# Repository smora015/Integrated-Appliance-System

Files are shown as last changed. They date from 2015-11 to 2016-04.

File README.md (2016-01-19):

# Integrated-Appliance-System
##### Controllers for an Energy Efficient, Sustainable Appliance System.

The Integrated Appliance System is a Senior Design, or capstone project for the Department of Chemical & Environmental Engineering for UC Riverside, under the advisory of Dr. Kawai Tam. We aim to draft, design, and potentially market an energy combination of appliances that cut your electricity bill substantially. It's common knowledge that appliances such as washers and dryers in typical residential homes are among the highest in terms of energy consumption. We're an interdisciplinary team that consists of Chemical, Environmental, Mechanical, and Computer Engineering majors. In a nut shell, the design utilizes solar thermal energy to heat up clothes, and taking the surplus energy to be routed into a water heater or into a home as warm air for heating, thus replacing a clothes dryer, water heater, and space heater. Being pretty savvy in embedded systems, I was reached out to implement a control system for the appliances. 

### Subsystems

##### IAS-PCB
Collection of Eagle PCB CAD files that contain prototype/production-ready schematic and board layouts for the IAS.

##### Integrated Appliance System
Contains the Atmel Project source for the ATmega1284-PU work.

##### Raspberry-Pi-Logger
Contains logic for a temporary method of controlling the IAS, utilizing startup scripts to log temperature and humidity data.

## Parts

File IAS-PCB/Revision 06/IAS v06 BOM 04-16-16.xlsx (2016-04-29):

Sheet: PCB BOM
Index | Store | Store Part # | Manufacturer Part # | Description | Device Packaging | Qty | Unit Price | Price | Comments
1 | Digikey | ATMEGA1284-PU-ND | ATMEGA1284-PU | Atmega1284 Microcontroller | Through-hole | 2 | $7.60 | $15.20 | Main Controllers
2 | Digikey | 296-1600-5-ND | 296-1600-5-ND | 8-bit Shift Register | Through-hole | 1 | $0.58 | $0.58 | Used to reduce amount of pins needed
3 | Digikey | 311-10KERCT-ND | RC1206JR-0710KL | 10K Ohm Resistor | 1206 | 2 | $0.10 | $0.20 | Pull-up resistors for Sensors
4 | Digikey | 311-1.00KFRCT-ND | RC1206FR-071KL | 1K Ohm Resistor | 1206 | 2 | $0.03 | $0.06 | Used for Bluetooth RX pin as voltage divider | `
5 | Digikey | 311-2.0KERCT-ND | RC1206JR-072KL | 2K Ohm Resistor | 1206 | 1 | $0.02 | $0.02 | Used for Bluetooth RX pin as voltage divider
6 | Digikey | 311-1356-1-ND | CC1206KKX7R8BB105 | 1 uF 25V Capacitor | 1206 | 2 | $0.12 | $0.24 | Stabilizes input voltage/current
7 | Digikey | 587-1353-1-ND | TMK316F106ZL-T | 10uF 25V Capacitor | 1206 | 2 | $0.26 | $0.51 | Stabilizes regulated voltage/current
8 | Digikey | 296-9213-5-ND | CD74HC4050E | 5V to 3.3V Level Shifter | 16DIP | 1 | $0.48 | $0.48 | Converts power to 3.3V for Nokia LCD
9 | Digikey | S7006-ND | PPTC081LFBN-RC | 8-pin header | Through-hole .1" | 7 | $0.66 | $4.65 | Header pins for component connections
10 | Digikey | S7004-ND | PPTC061LFBN-RC | 6-pin header | Through-hole .1" | 2 | $0.68 | $1.36 | Header pins for component connections
11 | Digikey | S7038-ND | PPPC051LFBN-RC | 5-pin header | Through-hole .1" | 2 | $0.65 | $1.30 | Header pins for component connections
12 | Digikey | S7002-ND | PPTC041LFBN-RC | 4-pin header | Through-hole .1" | 4 | $0.46 | $1.85 | Header pins for component connections
14 | Digikey | AZ1117EH-5.0TRG1DICT-ND | AZ1117EH-5.0TRG1 | 5V Fixed Voltage Regulator (16V Max Input @ 1A) | SOT-223 | 1 | $0.43 | $0.43 | Input regulator (5V)
15 | Digikey | CP-102A-ND | PJ-102B | 2.0mm DC barrel-power jack | Through-hole | 1 | $1.00 | $1.00 | Connector jack for power
16 | Digikey | 754-1724-ND | WP710A10SGD5V | Power Status LED | Through-hole | 1 | $0.44 | $0.44 | LED indicator for power on
17 | Digikey | AE9992-ND | A16-LC-TT | 16-DIP Socket | Through-hole | 2 | $0.25 | $0.50 | Allows non-solder connections for chips
18 | Digikey | 609-4716-ND | DILB40P-223TLF | 40-DIP Socket | Through-hole | 2 | $0.58 | $1.16 | Allows non-solder connections for chips
19 | OSH Park | N/A | OSHPark.com | PCB Board Manufacturing (3.54x2.30 inches) | 2-layer PCB | 1 | $40.65 | $40.65 | 3 Boards Included
 |  |  |  | Total |  |  |  | $70.63

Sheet: System BOM
Index | Store | Store Part # | Manufacturer Part # | Description | Device Packaging | Qty | Unit Price | Price | Comments | Remark
A | Amazon | Here (http://www.amazon.com/Nokia-5110-LCD-Screen/dp/B0068EUIXG) | 5110 | Nokia 5110 LCD | N/A | 1 | $6.60 | $6.60 | 5V IAS Controls Display | -
B | Amazon | Here (http://www.amazon.com/uxcell-Standard-Character-Backlight-Display/dp/B00EDMMTGY) | uxcell | 16x2 Backlit LCD | N/A | 1 | $7.69 | $7.69 | 5V IAS Status Display | -
C | Amazon | Here (http://www.amazon.com/gp/product/B00R4KGG6Q?psc=1&redirect=true&ref_=oh_aui_detailpage_o05_s00) | HT21 AM2301 | Temperature & Humidity Sensor | N/A | 3 | $8.60 | $25.80 | 5V Sensor with -40 - 80 deg C Range | Alternative - DHT 22
D | Amazon | Here (http://www.amazon.com/RioRand-Waterproof-Digital-Temperature-DS18b20/dp/B00KUNKR3M) | DS18B20 | Temperature Probe | N/A | 2 | $5.00 | $10.00 | 5V Sensor with -55 - 125 deg C Range | Optional
E | Amazon | Here (http://www.amazon.com/2013newestseller-HC-SR501-Pyroelectric-Infrared-Detector/dp/B00FDPO9B8) | PIR | Motion Sensor | N/A | 4 | $2.00 | $8.00 | 5V Sensor | -
F | Parallax | Here (https://www.parallax.com/product/27115) | SRD-05VDC | Relay Switch | N/A | 4 | $10.00 | $40.00 | Switch to power on fans | Find better price!
G | Amazon | Here (http://www.amazon.com/uxcell-Matrix-Keyboard-Keypad-Stamp/dp/B00HGAK2FK) | uxcell | Keypad | N/A | 1 | $4.00 | $4.00 | Keypad to control | -
H | Amazon | Here (http://www.amazon.com/JY-MCU-Arduino-Bluetooth-Wireless-Serial/dp/B009DZQ4MG) | JY-MCU | Bluetooth Wireless module | N/A | 1 | $6.50 | $6.50 | Allows for wireless control of IAS | -
 |  |  |  |  |  |  |  | $0.00
 |  |  |  |  |  |  |  | $0.00
 |  |  |  |  |  |  |  | $0.00
 |  |  |  |  |  |  |  | $0.00
 |  |  |  |  |  |  |  | $0.00
 |  |  |  |  |  |  |  | $0.00
 |  |  |  |  |  |  |  | $0.00
 |  |  |  |  |  |  |  | $0.00
 |  |  |  |  |  |  |  | $0.00
 |  |  |  |  |  |  |  | $0.00
 |  |  |  |  |  |  |  | $0.00
 |  |  |  |  |  |  |  | $0.00
 |  |  |  |  |  |  |  | $0.00
 |  |  |  |  |  |  |  | $0.00
 |  |  |  |  |  |  |  | $0.00
 |  |  |  |  |  |  |  | $0.00
 |  |  |  |  |  |  |  | $0.00
 |  |  |  |  |  |  |  | $0.00
 |  |  |  |  |  |  |  | $0.00
 |  |  |  |  |  |  |  | $0.00

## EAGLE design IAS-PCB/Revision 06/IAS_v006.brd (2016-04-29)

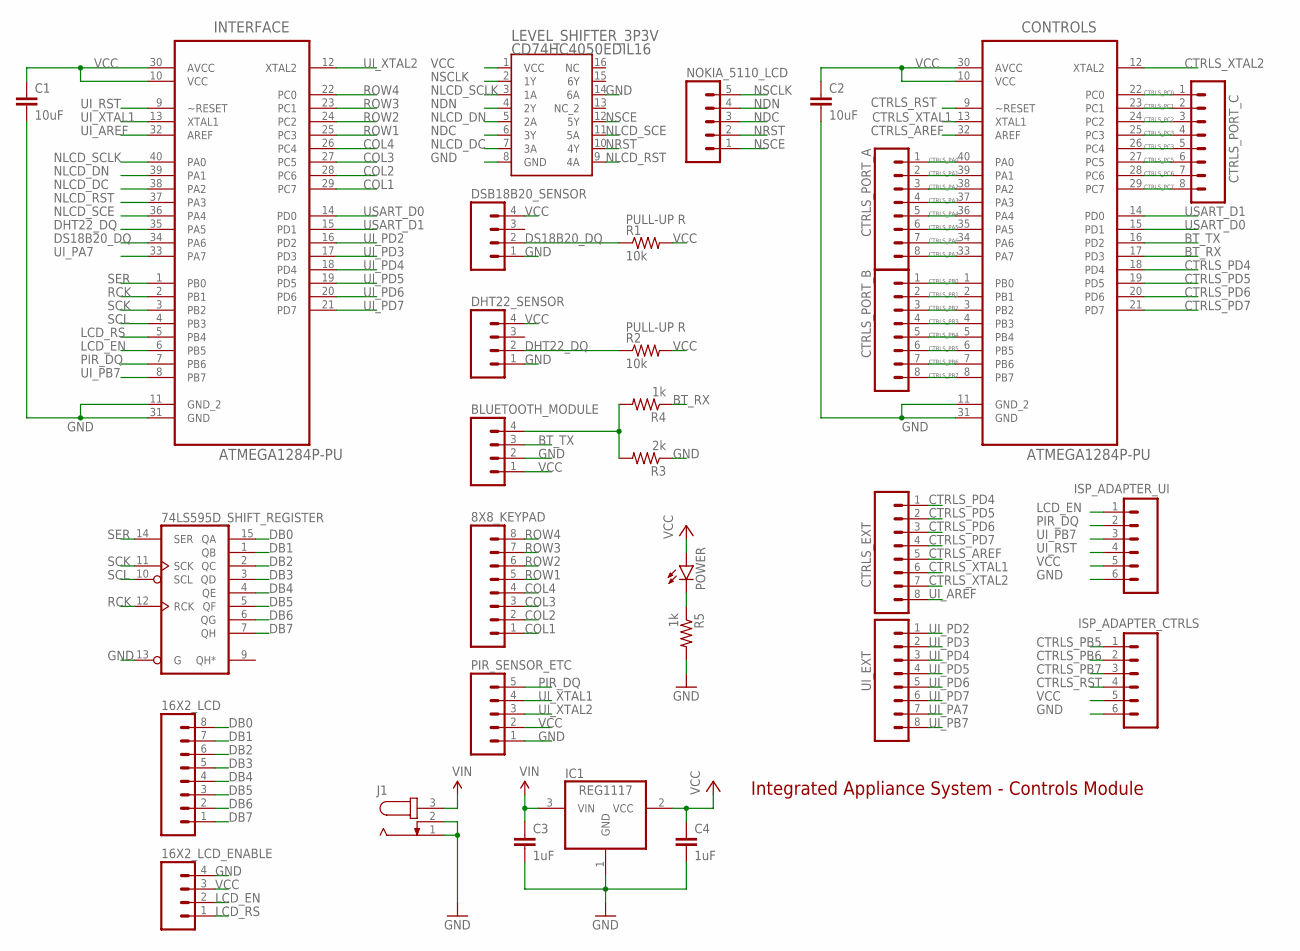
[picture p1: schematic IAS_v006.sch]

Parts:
8X8_KEYPAD, 16X2_LCD: M08; 1X08_ROUND
16X2_LCD_ENABLE: M04NO_SILK_ALL_ROUND; 1X04_NO_SILK_ALL_ROUND
74LS595D_SHIFT_REGISTER: 74LS595N; DIL16; MPN SN74LS595D
BLUETOOTH_MODULE: M04NO_SILK_ALL_ROUND; 1X04_NO_SILK_ALL_ROUND
C1, C2: 10uF; 1206
C3, C4: 1uF; 1206
CONTROLS: ATMEGA1284P-PU; DIP254P1524X483-40
CTRLS_EXT: M08; 1X08_ROUND
CTRLS_PORT_A: M08; 1X08_ROUND
CTRLS_PORT_B: M08; 1X08_ROUND
CTRLS_PORT_C: M08; 1X08_ROUND
DHT22_SENSOR: M04NO_SILK_ALL_ROUND; 1X04_NO_SILK_ALL_ROUND
DSB18B20_SENSOR: M04NO_SILK_ALL_ROUND; 1X04_NO_SILK_ALL_ROUND
IC1: REG1117; SOT223
INTERFACE: ATMEGA1284P-PU; DIP254P1524X483-40
ISP_ADAPTER_CTRLS: M06SILK_FEMALE_PTH; 1X06
ISP_ADAPTER_UI: M06SILK_FEMALE_PTH; 1X06
J1: JACK-PLUG0; SPC4077
LEVEL_SHIFTER_3P3V: CD74HC4050EDIL16; DIL16
NOKIA_5110_LCD: M05PTH; 1X05
PIR_SENSOR_ETC: M05PTH; 1X05
POWER: LED3MM
R1, R2: 10k; 1206
R3: 2k; 1206
R4, R5: 1k; 1206
UI_EXT: M08; 1X08_ROUND

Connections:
BT_RX: CONTROLS.17 (PD3), R4.1
BT_TX: BLUETOOTH_MODULE.3, CONTROLS.16 (PD2)
COL1: 8X8_KEYPAD.1, INTERFACE.29 (PC7)
COL2: 8X8_KEYPAD.2, INTERFACE.28 (PC6)
COL3: 8X8_KEYPAD.3, INTERFACE.27 (PC5)
COL4: 8X8_KEYPAD.4, INTERFACE.26 (PC4)
CTRLS_AREF: CONTROLS.32 (AREF), CTRLS_EXT.5
CTRLS_PA0: CONTROLS.40 (PA0), CTRLS_PORT_A.1
CTRLS_PA1: CONTROLS.39 (PA1), CTRLS_PORT_A.2
CTRLS_PA2: CONTROLS.38 (PA2), CTRLS_PORT_A.3
CTRLS_PA3: CONTROLS.37 (PA3), CTRLS_PORT_A.4
CTRLS_PA4: CONTROLS.36 (PA4), CTRLS_PORT_A.5
CTRLS_PA5: CONTROLS.35 (PA5), CTRLS_PORT_A.6
CTRLS_PA6: CONTROLS.34 (PA6), CTRLS_PORT_A.7
CTRLS_PA7: CONTROLS.33 (PA7), CTRLS_PORT_A.8
CTRLS_PB0: CONTROLS.1 (PB0), CTRLS_PORT_B.1
CTRLS_PB1: CONTROLS.2 (PB1), CTRLS_PORT_B.2
CTRLS_PB2: CONTROLS.3 (PB2), CTRLS_PORT_B.3
CTRLS_PB3: CONTROLS.4 (PB3), CTRLS_PORT_B.4
CTRLS_PB4: CONTROLS.5 (PB4), CTRLS_PORT_B.5
CTRLS_PB5: CONTROLS.6 (PB5), CTRLS_PORT_B.6, ISP_ADAPTER_CTRLS.1
CTRLS_PB6: CONTROLS.7 (PB6), CTRLS_PORT_B.7, ISP_ADAPTER_CTRLS.2
CTRLS_PB7: CONTROLS.8 (PB7), CTRLS_PORT_B.8, ISP_ADAPTER_CTRLS.3
CTRLS_PC0: CONTROLS.22 (PC0), CTRLS_PORT_C.1
CTRLS_PC1: CONTROLS.23 (PC1), CTRLS_PORT_C.2
CTRLS_PC2: CONTROLS.24 (PC2), CTRLS_PORT_C.3
CTRLS_PC3: CONTROLS.25 (PC3), CTRLS_PORT_C.4
CTRLS_PC4: CONTROLS.26 (PC4), CTRLS_PORT_C.5
CTRLS_PC5: CONTROLS.27 (PC5), CTRLS_PORT_C.6
CTRLS_PC6: CONTROLS.28 (PC6), CTRLS_PORT_C.7
CTRLS_PC7: CONTROLS.29 (PC7), CTRLS_PORT_C.8
CTRLS_PD4: CONTROLS.18 (PD4), CTRLS_EXT.1
CTRLS_PD5: CONTROLS.19 (PD5), CTRLS_EXT.2
CTRLS_PD6: CONTROLS.20 (PD6), CTRLS_EXT.3
CTRLS_PD7: CONTROLS.21 (PD7), CTRLS_EXT.4
CTRLS_RST: CONTROLS.9 (~RESET), ISP_ADAPTER_CTRLS.4
CTRLS_XTAL1: CONTROLS.13 (XTAL1), CTRLS_EXT.6
CTRLS_XTAL2: CONTROLS.12 (XTAL2), CTRLS_EXT.7
DB0: 16X2_LCD.8, 74LS595D_SHIFT_REGISTER.15 (QA)
DB1: 16X2_LCD.7, 74LS595D_SHIFT_REGISTER.1 (QB)
DB2: 16X2_LCD.6, 74LS595D_SHIFT_REGISTER.2 (QC)
DB3: 16X2_LCD.5, 74LS595D_SHIFT_REGISTER.3 (QD)
DB4: 16X2_LCD.4, 74LS595D_SHIFT_REGISTER.4 (QE)
DB5: 16X2_LCD.3, 74LS595D_SHIFT_REGISTER.5 (QF)
DB6: 16X2_LCD.2, 74LS595D_SHIFT_REGISTER.6 (QG)
DB7: 16X2_LCD.1, 74LS595D_SHIFT_REGISTER.7 (QH)
DHT22_DQ: DHT22_SENSOR.2, INTERFACE.35 (PA5), R2.1
DS18B20_DQ: DSB18B20_SENSOR.2, INTERFACE.34 (PA6), R1.1
GND: 16X2_LCD_ENABLE.4, 74LS595D_SHIFT_REGISTER.8 (GND), 74LS595D_SHIFT_REGISTER.13 (G), BLUETOOTH_MODULE.2, C1.2, C2.2, C3.2, C4.2, CONTROLS.11 (GND_2), CONTROLS.31 (GND), DHT22_SENSOR.1, DSB18B20_SENSOR.1, IC1.1 (GND), INTERFACE.11 (GND_2), INTERFACE.31 (GND), ISP_ADAPTER_CTRLS.6, ISP_ADAPTER_UI.6, J1.1, J1.2, LEVEL_SHIFTER_3P3V.8 (GND), LEVEL_SHIFTER_3P3V.14 (6A), PIR_SENSOR_ETC.1, R3.1, R5.2
LCD_EN: 16X2_LCD_ENABLE.2, INTERFACE.6 (PB5), ISP_ADAPTER_UI.1
LCD_RS: 16X2_LCD_ENABLE.1, INTERFACE.5 (PB4)
unnamed: POWER.K (C), R5.1
unnamed: BLUETOOTH_MODULE.4, R3.2, R4.2
NDC: LEVEL_SHIFTER_3P3V.6 (3Y), NOKIA_5110_LCD.3
NDN: LEVEL_SHIFTER_3P3V.4 (2Y), NOKIA_5110_LCD.4
NLCD_DC: INTERFACE.38 (PA2), LEVEL_SHIFTER_3P3V.7 (3A)
NLCD_DN: INTERFACE.39 (PA1), LEVEL_SHIFTER_3P3V.5 (2A)
NLCD_RST: INTERFACE.37 (PA3), LEVEL_SHIFTER_3P3V.9 (4A)
NLCD_SCE: INTERFACE.36 (PA4), LEVEL_SHIFTER_3P3V.11 (5A)
NLCD_SCLK: INTERFACE.40 (PA0), LEVEL_SHIFTER_3P3V.3 (1A)
NRST: LEVEL_SHIFTER_3P3V.10 (4Y), NOKIA_5110_LCD.2
NSCE: LEVEL_SHIFTER_3P3V.12 (5Y), NOKIA_5110_LCD.1
NSCLK: LEVEL_SHIFTER_3P3V.2 (1Y), NOKIA_5110_LCD.5
PIR_DQ: INTERFACE.7 (PB6), ISP_ADAPTER_UI.2, PIR_SENSOR_ETC.5
RCK: 74LS595D_SHIFT_REGISTER.12 (RCK), INTERFACE.2 (PB1)
ROW1: 8X8_KEYPAD.5, INTERFACE.25 (PC3)
ROW2: 8X8_KEYPAD.6, INTERFACE.24 (PC2)
ROW3: 8X8_KEYPAD.7, INTERFACE.23 (PC1)
ROW4: 8X8_KEYPAD.8, INTERFACE.22 (PC0)
SCK: 74LS595D_SHIFT_REGISTER.11 (SCK), INTERFACE.3 (PB2)
SCL: 74LS595D_SHIFT_REGISTER.10 (SCL), INTERFACE.4 (PB3)
SER: 74LS595D_SHIFT_REGISTER.14 (SER), INTERFACE.1 (PB0)
UI_AREF: CTRLS_EXT.8, INTERFACE.32 (AREF)
UI_PA7: INTERFACE.33 (PA7), UI_EXT.7
UI_PB7: INTERFACE.8 (PB7), ISP_ADAPTER_UI.3, UI_EXT.8
UI_PD2: INTERFACE.16 (PD2), UI_EXT.1
UI_PD3: INTERFACE.17 (PD3), UI_EXT.2
UI_PD4: INTERFACE.18 (PD4), UI_EXT.3
UI_PD5: INTERFACE.19 (PD5), UI_EXT.4
UI_PD6: INTERFACE.20 (PD6), UI_EXT.5
UI_PD7: INTERFACE.21 (PD7), UI_EXT.6
UI_RST: INTERFACE.9 (~RESET), ISP_ADAPTER_UI.4
UI_XTAL1: INTERFACE.13 (XTAL1), PIR_SENSOR_ETC.4
UI_XTAL2: INTERFACE.12 (XTAL2), PIR_SENSOR_ETC.3
USART_D0: CONTROLS.15 (PD1), INTERFACE.14 (PD0)
USART_D1: CONTROLS.14 (PD0), INTERFACE.15 (PD1)
VCC: 16X2_LCD_ENABLE.3, 74LS595D_SHIFT_REGISTER.16 (VCC), BLUETOOTH_MODULE.1, C1.1, C2.1, C4.1, CONTROLS.10 (VCC), CONTROLS.30 (AVCC), DHT22_SENSOR.4, DSB18B20_SENSOR.4, IC1.2 (VCC), INTERFACE.10 (VCC), INTERFACE.30 (AVCC), ISP_ADAPTER_CTRLS.5, ISP_ADAPTER_UI.5, LEVEL_SHIFTER_3P3V.1 (VCC), PIR_SENSOR_ETC.2, POWER.A, R1.2, R2.2
VIN: C3.1, IC1.3 (VIN), J1.3

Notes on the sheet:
PULL-UP R
Integrated Appliance System - Controls Module

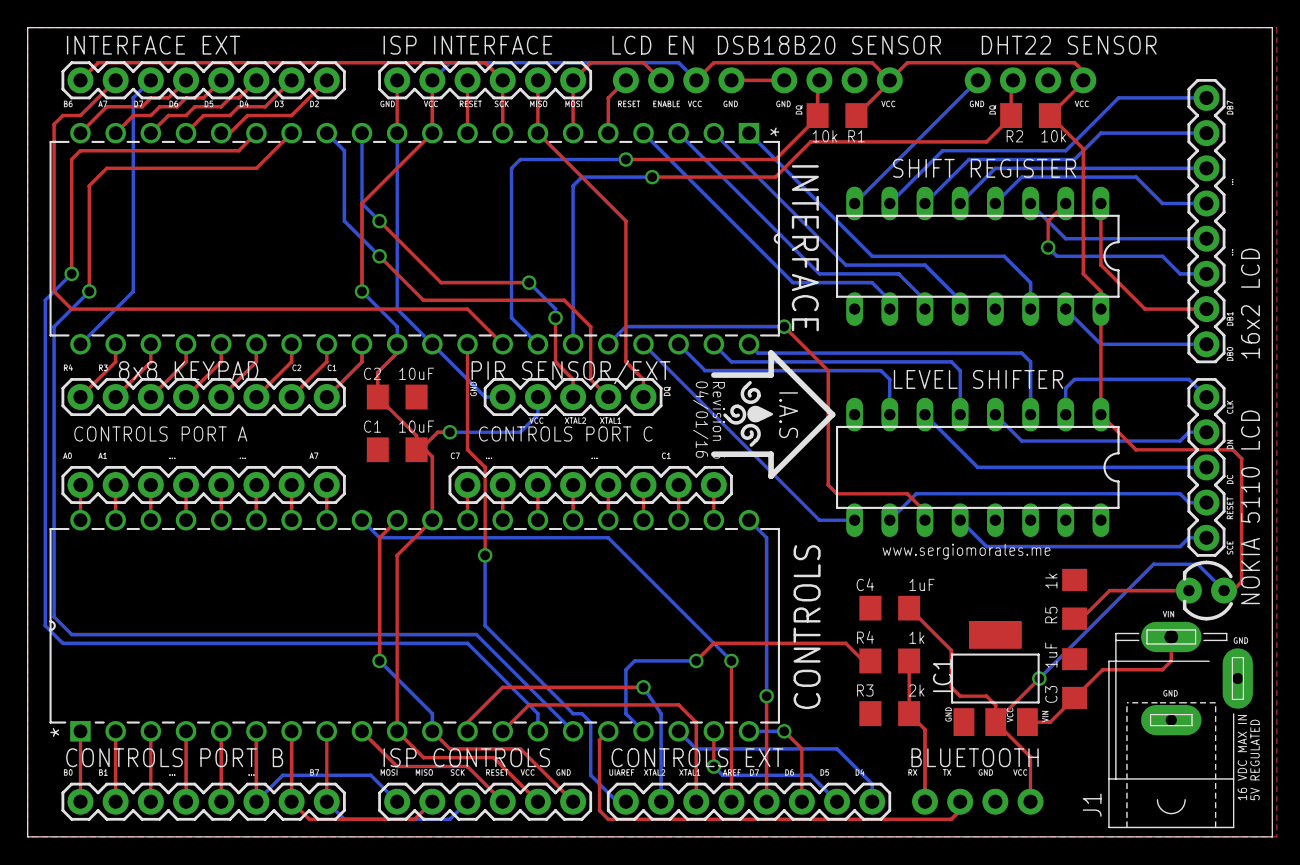
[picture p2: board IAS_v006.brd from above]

Board: 2 copper layers, 89.8 x 58.4 mm, 31 parts (0 on the bottom side), 88 nets.

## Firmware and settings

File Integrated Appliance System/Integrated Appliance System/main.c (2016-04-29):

#include <stdint.h> 
#include <stdlib.h> 
#include <stdio.h> 
#include <stdbool.h> 
#include <string.h> 
#include <math.h> 

// AVR Include Files
#define F_CPU 8000000UL     // 8Mhz Clock
#include <util/delay.h>
#include <avr/io.h>         
#include <avr/interrupt.h> 
#include <avr/eeprom.h> 
#include <avr/portpins.h> 
#include <avr/pgmspace.h> 

// IAS macro and pinout definitions
#include "ias_pinout.h"
#include "display/lumex_lcd.h"
#include "com/shift_reg.h"

int main(void) 
{
	DDRA = 0xFF; PORTA = 0x00; // Nokia LCD: 0-4. DHT22: 5. DS18B20: 6.
	DDRB = 0xFF; PORTB = 0x00; // 16x2 LCD on Shift Registers
	DDRC = 0xF0; PORTC = 0x0F; // Keypad
	DDRD = 0xFF; PORTD = 0x00; // USART interface
	
    LCD_init();

	for(;;)
	{
		LCD_DisplayString(3, (const unsigned char*) "Hello World!", 0);
        
        //_delay_ms(1000);       // Delay logic for 100 ms
		
		//PORTD ^= 0xFF; // UI PORTD bits
			
	}
		
	return 0; 
}


//// FreeRTOS Include Files
//#include "FreeRTOS.h"
//#include "task.h"
//#include "croutine.h"
//#include "usart_ATmega1284.h"

//void ControlTask()
//{
//for( ;; )
//{
//Control_Tick();
//vTaskDelay(1);
//}
//}
//
//void StartSecPulse(unsigned portBASE_TYPE Priority)
//{
//xTaskCreate(ControlTask, (signed portCHAR *)"ControlTask", configMINIMAL_STACK_SIZE, NULL, Priority, NULL );
//}

	//#ifdef main2
	//DDRB = 0xFF; PORTB = 0x00; // Fans (0)
	//DDRC = 0xFF; PORTC = 0x00; // LEDS
	//DDRA = 0xFF; PORTA = 0x00; // Motor
	//initUSART(1);			   // Bluetooth
	//initUSART(0);			   // IAS
	//USART_Flush(0);
	//USART_Flush(1);
	//
	//// Start Tasks
	//StartSecPulse(1);
	//
	//// Run Scheduler
	//vTaskStartScheduler();
	//#else
	//DDRA = 0xFF; PORTA = 0x00; // Nokia LCD: 0-4. DHT22: 5. DS18B20: 6.
	//DDRB = 0xFF; PORTB = 0x00; // 16x2 LCD on Shift Registers
	//DDRC = 0xF0; PORTC = 0x0F; // Keypad
	//DDRD = 0xFF; PORTD = 0x00; // USART interface
	//
	//while(1)
	//{
	//
	//IAS_MenuTick();
	//_delay_ms(1);
	//}
	//#endif

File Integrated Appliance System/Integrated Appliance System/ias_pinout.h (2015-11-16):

/*
 * ias_pinout.h
 *
 * Created: 10/12/2015 9:33:00 PM
 *  Author: Sergio
 *
 *  Description: Defines the pinout for all ports 
 */ 



#ifndef IAS_PINOUT_H_
#define IAS_PINOUT_H_
    
    #include <avr/io.h>
    
    /* ============== Communication ============== */

    // 4x4 Keypad { keypad.h }
    #define KEYPADPORT PORTC
    #define KEYPADPIN  PINC
    #define ROW1 3
    #define ROW2 2
    #define ROW3 1
    #define ROW4 0
    #define COL1 7
    #define COL2 6
    #define COL3 5
    #define COL4 4

    // Shift Register { shift_reg.h }
    #define SHIFT_PORT PORTB
    #define SER_PIN   0
    #define RCLK_PIN  1
    #define SRCLK_PIN 2
    #define SRCLR_PIN 3

    /* ============== Sensors ============== */

    // DHT22 Temp/Humidity Sensor { dht22.h }
    #define DHT_DDR DDRA
    #define DHT_PORT PORTA
    #define DHT_PIN PINA
    #define DHT_INPUTPIN 5

    // DS18B20 Temperature Probe { ds18b20.h }
    #define DS18B20_PORT PORTA
    #define DS18B20_DDR  DDRA
    #define DS18B20_PIN  PINA
    #define DS18B20_DQ   6
    
    // PIR Motion Sensor { pir.h }
    #define PIR_DDR  DDRB
    #define PIR_READ PINB
    #define PIR_PIN  6

    /* ============== Display ============== */

    // 16x2 LUMEX LCD { lumex_lcd.h }
    //#define DATA_BUS PORTB          // port connected to pins 7-14 of LCD display | WE NOW USE SHIFT REGISTERS ON DEFINED PINS
    #define CONTROL_BUS PORTB	      // port connected to pins 4 and 6 of LCD disp.
    #define RS 4			          // pin number of uC connected to pin 4 of LCD disp.
    #define E 5			              // pin number of uC connected to pin 6 of LCD disp.

    // NOKIA 84x48 PCD8544 LCD { pcd8544.h }
    #define LCD_PORT            PORTA
    #define LCD_SCE_HI			LCD_PORT |= (1<<4)
    #define LCD_SCE_LO			LCD_PORT &= ~(1<<4)
    #define LCD_RST_HI			LCD_PORT |= (1<<3)
    #define LCD_RST_LO			LCD_PORT &= ~(1<<3)
    #define LCD_DC_HI			LCD_PORT |= (1<<2)
    #define LCD_DC_LO			LCD_PORT &= ~(1<<2)
    #define LCD_DN_HI			LCD_PORT |= (1<<1)
    #define LCD_DN_LO			LCD_PORT &= ~(1<<1)
    #define LCD_SCLK_HI			LCD_PORT |= (1<<0)
    #define LCD_SCLK_LO			LCD_PORT &= ~(1<<0)
    //#define LCD_BACKLIGHT_HI	LCD_PORT |= (1<<5)   // Optional
    //#define LCD_BACKLIGHT_LO	LCD_PORT &= ~(1<<5)  // Optional
    
    #define LCD_C 0 // Command
    #define LCD_D 1 // Data

    #define LCD_WIDTH	84
    #define LCD_HEIGHT	48

#endif /* IAS_PINOUT_H_ */

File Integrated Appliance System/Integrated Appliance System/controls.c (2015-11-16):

/*
 * controls.c
 *
 * Created: 12/15/2014 7:00:38 PM
 *  Author: Sergio
 */ 
#include "controls.h"
#include "com/usart_ATmega1284.h"
#include <avr/io.h>
#include <stdlib.h>

unsigned char step_count = 0x00;
unsigned char  steps[8] = { 0x01, 0x03, 0x02, 0x06, 0x04, 0x0C, 0x08, 0x09 };	// Clockwise phases
unsigned char bsteps[8] = { 0x09, 0x08, 0x0C, 0x04, 0x06, 0x02, 0x03, 0x01  };  // Counter-Clockwise phases
int count = 0;																	// Counter for number of phases

char temp;
char message[100];

void USART_send_string( const char* string )
{
	USART_Flush(1);
	USART_Flush(0);
	int index = 0;
	while( string[index] )
	{
		USART_Send(string[index], 1);
		++index;
	}
}

enum control_states { init, receive, actuate_gears, disable_gears, actuate_fans, disable_fans, send_report } control_state;
void Control_Tick()
{
	// Mealy FSM (actions and transitions)
	switch( control_state )
	{
		case init:
			report = (char*) malloc(sizeof(char));
			control_state = receive;
			break;
			
		case receive:
			if( USART_HasReceived(0) )
				usart_byte = USART_Receive(0);
			else
				usart_byte = 0x00;
				
			if( USART_HasReceived(1) )
				bluetooth_byte = USART_Receive(1);
			else
				bluetooth_byte = 0x00;
				
			PORTC = usart_byte;
	
			if(usart_byte == ENABLE_MOTORH || bluetooth_byte == ENABLE_MOTORH)
			{
				count = 0;
				control_state = actuate_gears; // TRANSITION: actuate_gears;
			}
			else if(usart_byte == DISABLE_MOTORH || bluetooth_byte == DISABLE_MOTORH)
			{
				count = 0;
				control_state = disable_gears; // TRANSITION: disable_gears;
			}
			else if(usart_byte == ENABLE_FAND || bluetooth_byte == ENABLE_FAND)
			{
				control_state = actuate_fans;  // TRANSITION: actuate_fans
			}
			else if(usart_byte == DISABLE_FAND || bluetooth_byte == DISABLE_FAND)
			{
				control_state = disable_fans;  // TRANSITION: disable_fans
			}
			else if( usart_byte == SEND_REPORT)
			{
				control_state = send_report;
			}
			break;

		case actuate_gears:
			if( count < THREE_SIXTY) // Turn gears 180 degrees
			{
				PORTA = steps[ (step_count++ % 8) ];
				++count;			
			}
			else
			{
				count = 0;
				control_state = receive; // TRANSITION: receive
			}
			break;
		
		case disable_gears:
			if( count < THREE_SIXTY) // Turn gears 180 degrees
			{
				PORTA = bsteps[ (step_count++ % 8) ];
				++count;
			}
			else
			{
				count = 0;
				control_state = receive; // TRANSITION: receive
			}
			break;

		case actuate_fans:
			PORTB = 0x01;
			control_state = receive;
			break;
		
		case disable_fans:
			PORTB = 0x00;
			control_state = receive;
			break;
			
		case send_report:
			count = 0;
			do 
			{
				temp = USART_Receive(0);
				message[count++] = temp;
			} while (temp != 0xFF);
			
			USART_send_string(message);
			count = 0;
			break;
		default:
			control_state = init;
			break;
	}
}

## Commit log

2015-11-16 Added PCB CAD files and reorganized
    IAS PCB revision .05 finished. Started working on Atmel project as well.
    [IAS_BOM.xlsx, IAS_v005.brd, IAS_v005.sch]
2016-04-29 Revive Atmel Studio Project & Update RPI Code
    Update code to work with IAS Revision 06 PCB.
    Update Raspberry Pi DHT 22 Logger code.
    [IAS v06 BOM 04-16-16.xlsx, IAS_BOM.xlsx, IAS_v005.brd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]

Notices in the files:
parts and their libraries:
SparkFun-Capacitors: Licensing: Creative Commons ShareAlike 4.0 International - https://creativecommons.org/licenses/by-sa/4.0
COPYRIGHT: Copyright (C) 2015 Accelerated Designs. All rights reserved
